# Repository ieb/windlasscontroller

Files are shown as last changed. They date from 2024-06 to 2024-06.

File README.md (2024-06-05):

# Windlass Remote Control

I have found that wire windlass switches fail at when installed at the bow due to water ingress into the switches as do sockets. So 7 years ago I used a simple 433Mhz garage door controller as a remote windlass controller. However the remote controls are not easy to use being too small, and the range is typically less than 10m which is shorter than the boat making the controller unreliable.

This project uses a JDY-40 module (typical cost < $1) which can be configured as a remote 8 channel switch. It has a claimed range of 120m, tested at 60m and uses 2.4GHz. It sleeps automatically drawing 5uA when sleeping and requires almost no external components in the controller. The base uses a second JDY-40 module with opto couplers and a G1 transistor driving a relay.  Remote is powered by a CR123A 3V lithium battery which should last several years even if left on sleeping. There is an on-off switch. No custom code, but the modules have to be programmed as transmitter and base with the same RF IDs. Code to do this is in setup. 

There are 2 schematics, one for base and one for the controller, and designs for the case and base cases. 

The PCBs are in KiCad, and were milled using pcb2gcode double sided with alignment, see createGCode.sh for the setup. Everything else is very standard.

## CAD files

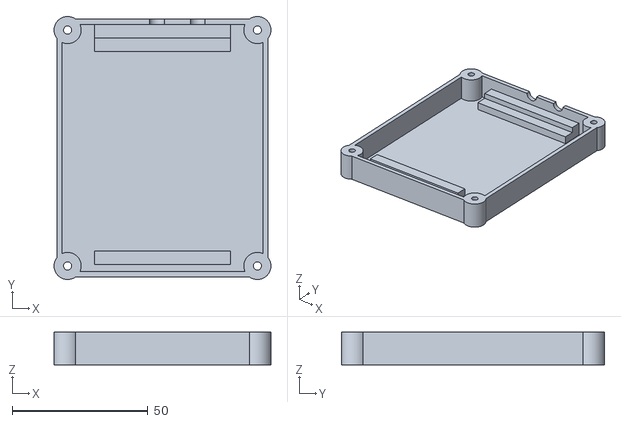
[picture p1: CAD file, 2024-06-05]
basecase/case.stl
80.0 x 97.0 x 12.0

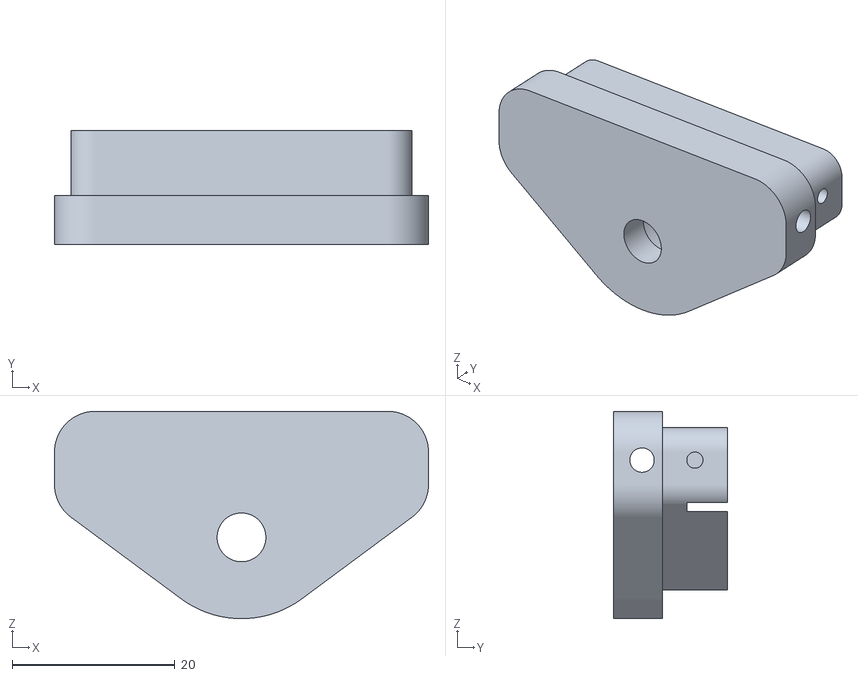
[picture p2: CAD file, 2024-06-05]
case2/cap.stl
46.0 x 14.0 x 25.5

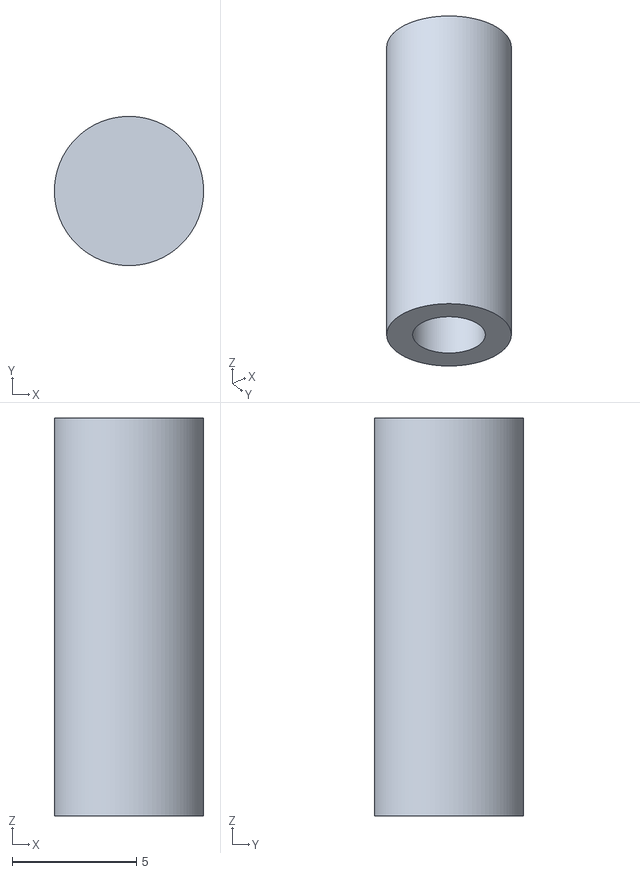
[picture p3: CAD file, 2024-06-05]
basecase/button.stl
6.00 x 6.00 x 16.0

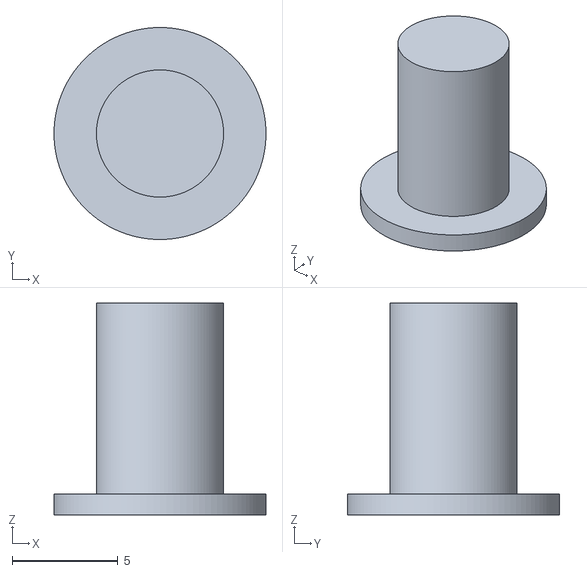
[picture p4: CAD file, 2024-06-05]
case2/onoff.stl
10.0 x 10.0 x 10.0

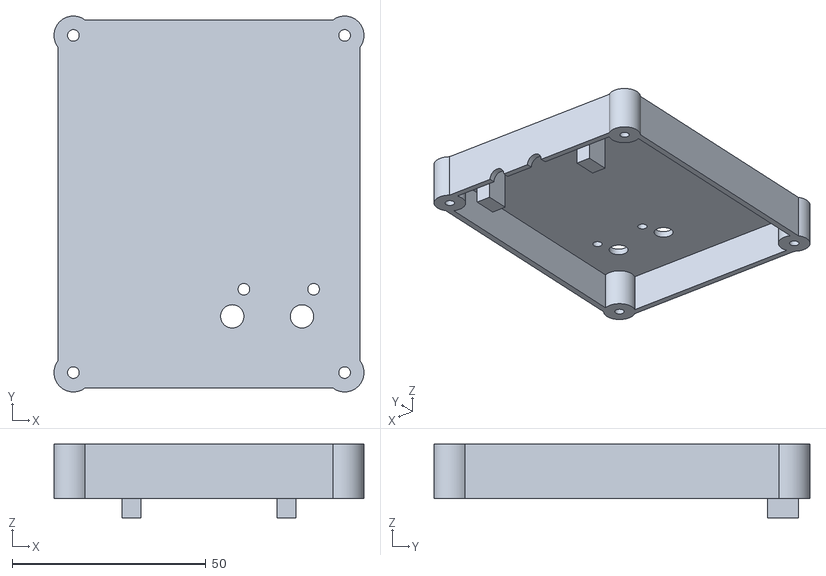
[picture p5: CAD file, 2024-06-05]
basecase/lid.stl
80.0 x 97.0 x 19.0

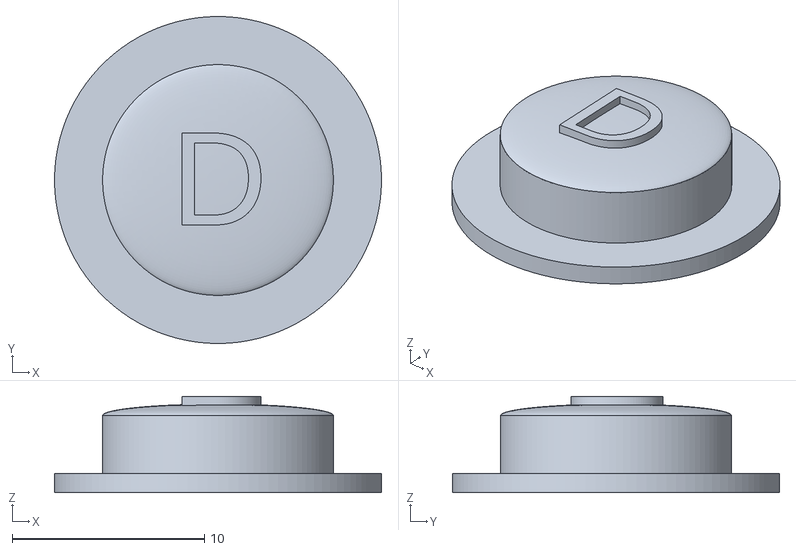
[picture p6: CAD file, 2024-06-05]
case2/down.stl
17.0 x 17.0 x 5.00

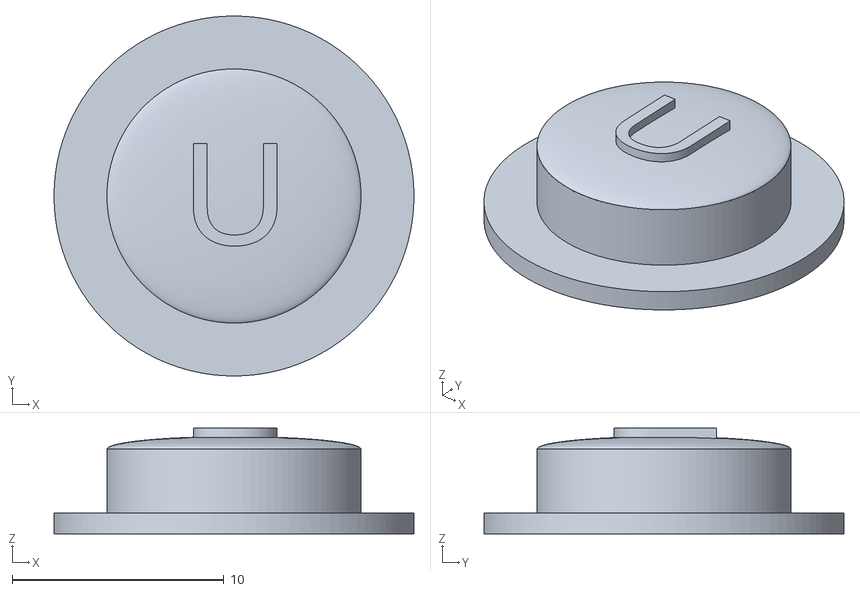
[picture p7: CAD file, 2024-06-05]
case2/up.stl
17.0 x 17.0 x 5.00

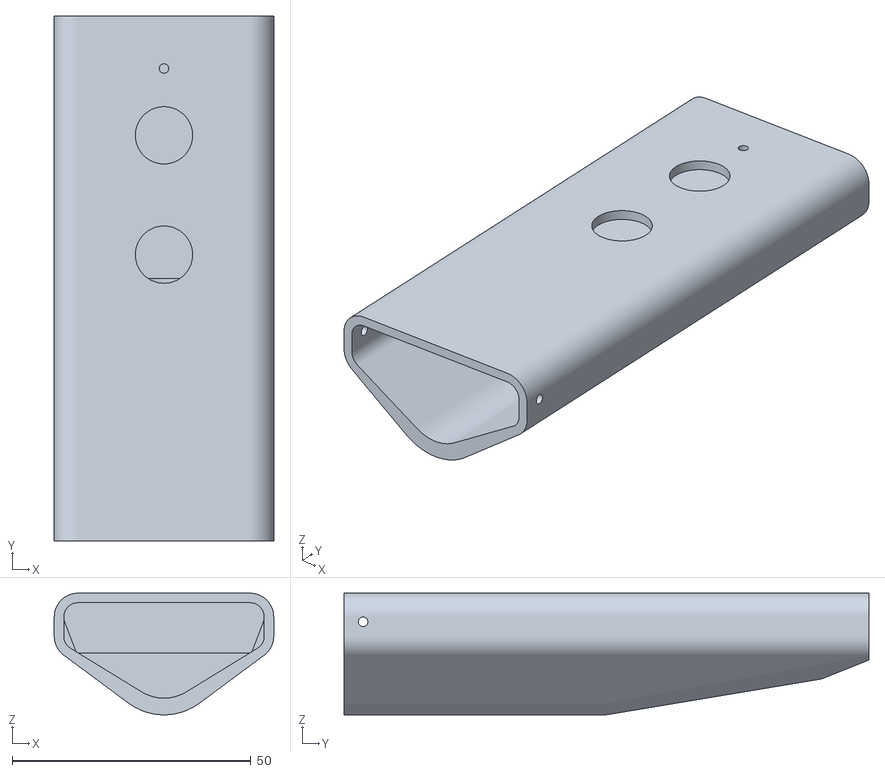
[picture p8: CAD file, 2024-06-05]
case2/case2.stl
46.0 x 110.0 x 25.5

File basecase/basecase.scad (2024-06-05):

$fn=100;




module board() {
    difference() {
    union() {
       translate([0,0,1])
        cube([60,81,2], center=true);
       // connectors
        color("blue") {
       translate([(30-17),40-9.8,15/2])
        cube([10,7.5,12], center=true);
       translate([(30-32),40-9.8,15/2])
        cube([10,7.5,12], center=true);
       // relays
       translate([(30-12),40-34,17/2])
        cube([19,19,17],center=true); 
       translate([(30-31),40-34,17/2])
        cube([19,19,17],center=true); 
        }
        
       
        // button
       translate([30-6,40-69,0])
         cylinder(d=3,h=14);
        // button
       translate([30-24,40-69,0])
         cylinder(d=3,h=14);

        // led
       translate([30-3,40-62,0])
         cylinder(d=2,h=14);
       translate([30-21,40-62,0])
         cylinder(d=2,h=14);
       
       
        
        }
    }
}
module lid(w=78,d=95,h=14,t=2) {
   difference() {
     translate([0,0,12+h/2-(t/2)]) 
      difference() {
        union() {
            difference() {
                union() {
                    cube([w-t*2,d,h], center=true);
                    cube([w,d-t*2,h], center=true);
                    translate([w/2-t,d/2-t,0])
                    cylinder(r=t,h=h, center=true);
                    translate([-(w/2-t),d/2-t,0])
                    cylinder(r=t,h=h, center=true);
                    translate([-(w/2-t),-(d/2-t),0])
                    cylinder(r=t,h=h, center=true);
                    translate([w/2-t,-(d/2-t),0])
                    cylinder(r=t,h=h, center=true);
                    

                }
                // inside
                translate([0,0,-t*2])
                    cube([w-t*2,d-t*2,h+t*2], center=true);
            }
            
            
           translate([-20,41.5,-2.5]) 
            cube([5,8,19], center=true);
           translate([20,41.5,-2.5]) 
            cube([5,8,19], center=true);

            
            // fxings
            translate([w/2-2*t,d/2-2*t,0])
                    cylinder(r=5,h=h, center=true);
            translate([-(w/2-2*t),d/2-2*t,0])
                    cylinder(r=5,h=h, center=true);
            translate([-(w/2-2*t),-(d/2-2*t),0])
                    cylinder(r=5,h=h, center=true);
                    translate([w/2-2*t,-(d/2-2*t),0])
                    cylinder(r=5,h=h, center=true);
        }
        
            translate([w/2-2*t,d/2-2*t,0])
                    cylinder(d=3,h=h+10, center=true);
            translate([-(w/2-2*t),d/2-2*t,0])
                    cylinder(d=3,h=h+10, center=true);
            translate([-(w/2-2*t),-(d/2-2*t),0])
                    cylinder(d=3,h=h+10, center=true);
                    translate([w/2-2*t,-(d/2-2*t),0])
                    cylinder(d=3,h=h+10, center=true);
    }
      cables();
    


        // button
       translate([30-6,40-69,0])
         cylinder(d=6,h=44);
        // button
       translate([30-24,40-69,0])
         cylinder(d=6,h=44);

        // led
       translate([30-3,40-62,0])
         cylinder(d=3,h=44);
       translate([30-21,40-62,0])
         cylinder(d=3,h=44);

       


    }

}

module case(w=78,d=95,h=12,t=2) {
   difference() {
   translate([0,0,(h/2)-(t/2)]) 
      difference() {
        union() {
            difference() {
                union() {
                    cube([w-t*2,d,h], center=true);
                    cube([w,d-t*2,h], center=true);
                    translate([w/2-t,d/2-t,0])
                    cylinder(r=t,h=h, center=true);
                    translate([-(w/2-t),d/2-t,0])
                    cylinder(r=t,h=h, center=true);
                    translate([-(w/2-t),-(d/2-t),0])
                    cylinder(r=t,h=h, center=true);
                    translate([w/2-t,-(d/2-t),0])
                    cylinder(r=t,h=h, center=true);
                    

                }
                // inside
                translate([0,0,t])
                    cube([w-t*2,d-t*2,h+t], center=true);
            }
            
             // pillars
            difference() {
            translate([0,-40.5,0])
            cube([50,5,10], center=true);
                translate([0,-38,0])            
                cube([55,5,3], center=true);
            }
            difference() {
                translate([0,40.5,-2])            
                cube([50,10,6], center=true);
                translate([0,38,0.5])            
                cube([55,5,4], center=true);
            }

            // fxings
            translate([w/2-2*t,d/2-2*t,0])
                    cylinder(r=5,h=h, center=true);
            translate([-(w/2-2*t),d/2-2*t,0])
                    cylinder(r=5,h=h, center=true);
            translate([-(w/2-2*t),-(d/2-2*t),0])
                    cylinder(r=5,h=h, center=true);
                    translate([w/2-2*t,-(d/2-2*t),0])
                    cylinder(r=5,h=h, center=true);
        }
        
            translate([w/2-2*t,d/2-2*t,0])
                    cylinder(d=3,h=h+10, center=true);
            translate([-(w/2-2*t),d/2-2*t,0])
                    cylinder(d=3,h=h+10, center=true);
            translate([-(w/2-2*t),-(d/2-2*t),0])
                    cylinder(d=3,h=h+10, center=true);
                    translate([w/2-2*t,-(d/2-2*t),0])
                    cylinder(d=3,h=h+10, center=true);
        }
        cables();
        
        
    }
}
module cables() {
    /*
    translate([-90,-15,10])
    rotate([0,90,0])
    cylinder(d=2,h=90);
    
    translate([-90,15,10])
    rotate([0,90,0])
    cylinder(d=4,h=90);
*/
            translate([13,0,11])
            rotate([-90,0,0])
                cylinder(d=5.5,h=55);

            translate([-2,0,11])
            rotate([-90,0,0])
                cylinder(d=5.5,h=55);


/*
    translate([-90,0,0])
    rotate([0,90,0])
    cylinder(d=4,h=90);

    color("red")
    translate([0,0,0])
    rotate([0,90,0])
    cylinder(d=7,h=90);
    */
}





difference() {
    union() {
        translate([0,0,4]) 
        board();
        color("blue") case();
        lid();
         //cables();
    }
   //translate([40,0,0])
   //cube([80,160,140], center=true);
}


//cables();
//translate([0,0,0]) 
//board();
//color("blue") case();
//lid();
//cables();

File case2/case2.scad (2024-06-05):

$fn=100;
module aaaBattery() {
    cylinder(d=10.5,h=44);
    translate([12,0,0])
    cylinder(d=10.5,h=44);
}

module aaBattery() {
    translate([8,0,0])
    cylinder(d=14.5,h=50.5);
    translate([-8,0,0])
    cylinder(d=14.5,h=50.5);
}

module cr123ABattery() {
    cylinder(d=17,h=35);
}

module cr2Battery() {
translate([0,0,0])
rotate([90,0,0])
    cylinder(d=15.6,h=27);
}
module switch(on=0,w=6,h=6) {
    cylinder(d=3.3,h=h-(on*0.8));
    translate([0,0,2]) {
        cube([w+0.3,w+0.3,4], center=true);
    }
}

module onoff(on=0) {
    cylinder(d=4,h=14-(3.5*on));
    translate([0,0,3.5]) {
        cube([7,7,7], center=true);
    }
}

module button(value) {
    difference() {
        union() {
            cylinder(d=17,h=1);
            cylinder(d=12,h=4);
            translate([0,0,4])
            scale([1,1,0.1])
               sphere(d=12);
            translate([0,0,4])
                linear_extrude(1)
                    text(value, size=5,  halign="center", valign="center");

        };
        //cylinder(d=5,h=2);
    }
}
module onoffButton() {
    difference() {
        union() {
            cylinder(d=10,h=1);
            cylinder(d=6,h=10);
            translate([0,0,9])
            scale([1,1,0.1])
               sphere(d=6);
        };
        cylinder(d=3,h=3);
        //cube([100,100,100]);
    }
}

module jdy40() {
    translate([0,0,2.5]) 
    cube([14,22,1],center=true);
}

module led() {
   translate([0,0,0])
   cylinder(d=2,h=12);
}
    


module board2() {
   translate([0,0,-2]) {
           
        translate([0,0,-1])
           cube([36,102,2],center = true);
       
   // top surface of the board is datum
         on = 0;
        translate([0,5,0]) {
           switch(on);
           translate([0,0,6.1-(on*0.8)])
               button("D");
         }
         translate([0,30,0]) {
           switch(on);  
           translate([0,0,6.1-(on*0.8)])
               button("U");
         }

         
         translate([0,17,-1.5])
           rotate([0,0,90])
               jdy40();
         
         translate([0,-44,-5.5]) {
             rotate([90,0,0]) {
                onoff(on);
                translate([0,0,11.5-(on*3.5)])
                    onoffButton();
             }
         }
         
         translate([0,44,0])
            led();
         
         translate([0,-4,-2])
          rotate([90,0,0])
            cr123ABattery();

       }
   
}


module case2() {
   difference() {
translate([0,55,-5])
  rotate([90,0,0])  {
 difference() {
     
      hull() {
          
       union() {   
        translate([0,0,55]) {
        cylinder(d=25,h=55);
        translate([18,8,0])
            cylinder(d=10,h=55);    
        translate([-18,8,0])
            cylinder(d=10,h=55);
        translate([18,4,0])
            cylinder(d=10,h=55);    
        translate([-18,4,0])
            cylinder(d=10,h=55);
        }
        
        translate([0,0,10]) {
              cylinder(d=10,h=55);
        }
        translate([18,8,0])
            cylinder(d=10,h=110);    
        translate([-18,8,0])
            cylinder(d=10,h=110);
        translate([18,4,0])
            cylinder(d=10,h=110);    
        translate([-18,4,0])
            cylinder(d=10,h=110);
        
           
       }
   
      }
      translate([0,0,55])    
      hull() {
        cylinder(d=18,h=56);
        translate([18,8,0])
            cylinder(d=6,h=56);    
        translate([-18,8,0])
            cylinder(d=6,h=56);
        translate([18,4,0])
            cylinder(d=6,h=56);    
        translate([-18,4,0])
            cylinder(d=6,h=56);
      }    
      translate([0,0,3])    
      hull() {
        translate([18,8,0])
            cylinder(d=6,h=55);    
        translate([-18,8,0])
            cylinder(d=6,h=55);
        translate([18,1,0])
            cylinder(d=1,h=55);    
        translate([-18,1,0])
            cylinder(d=1,h=55);
      }
      
      // screw holes
          translate([20,7,106])
          rotate([0,90,0])
              cylinder(d=2,h=10, center=true);
          translate([-20,7,106])
          rotate([0,90,0])
              cylinder(d=2,h=10, center=true);
    }


  }
  board2();
  }
}

module cap() {
translate([0,-55,-5])
  rotate([90,0,0]) {
      difference() {
      union() {

          hull() {
            cylinder(d=25,h=6);
            translate([18,8,0])
                cylinder(d=10,h=6);    
            translate([-18,8,0])
                cylinder(d=10,h=6);
            translate([18,4,0])
                cylinder(d=10,h=6);    
            translate([-18,4,0])
                cylinder(d=10,h=6);
       
          }
          translate([0,0,-8])    
          hull() {
            cylinder(d=18,h=13);
            translate([18,8,0])
                cylinder(d=6,h=13);    
            translate([-18,8,0])
                cylinder(d=6,h=13);
            translate([18,4,0])
                cylinder(d=6,h=13);    
            translate([-18,4,0])
                cylinder(d=6,h=13);
          } 
        }
        // button hole
        translate([0,-2.5,-9])
        cylinder(h=11,d=11);
        translate([0,-2.5,-8])
        cylinder(h=20,d=6);

        // board cutout
        translate([0,2.2,-8])
        cube([40,3,10], center=true);
        
        // scrw holes
        translate([20,7,-4])
          rotate([0,90,0])
              cylinder(d=2,h=10, center=true);
          translate([-20,7,-4])
          rotate([0,90,0])
              cylinder(d=2,h=10, center=true);

        // lanyard
        translate([00,7,2.5])
          rotate([0,90,0])
              cylinder(d=3,h=60, center=true);

        
    }
        
  }   
}

/*
board2();


difference()  {
    union() {
   cap();
   case2();
    }
  translate([0,-75,-75])
     cube([150,150,150]);
}
*/

//cap();
case2();
//button("D");
//button("U");
//onoffButton();

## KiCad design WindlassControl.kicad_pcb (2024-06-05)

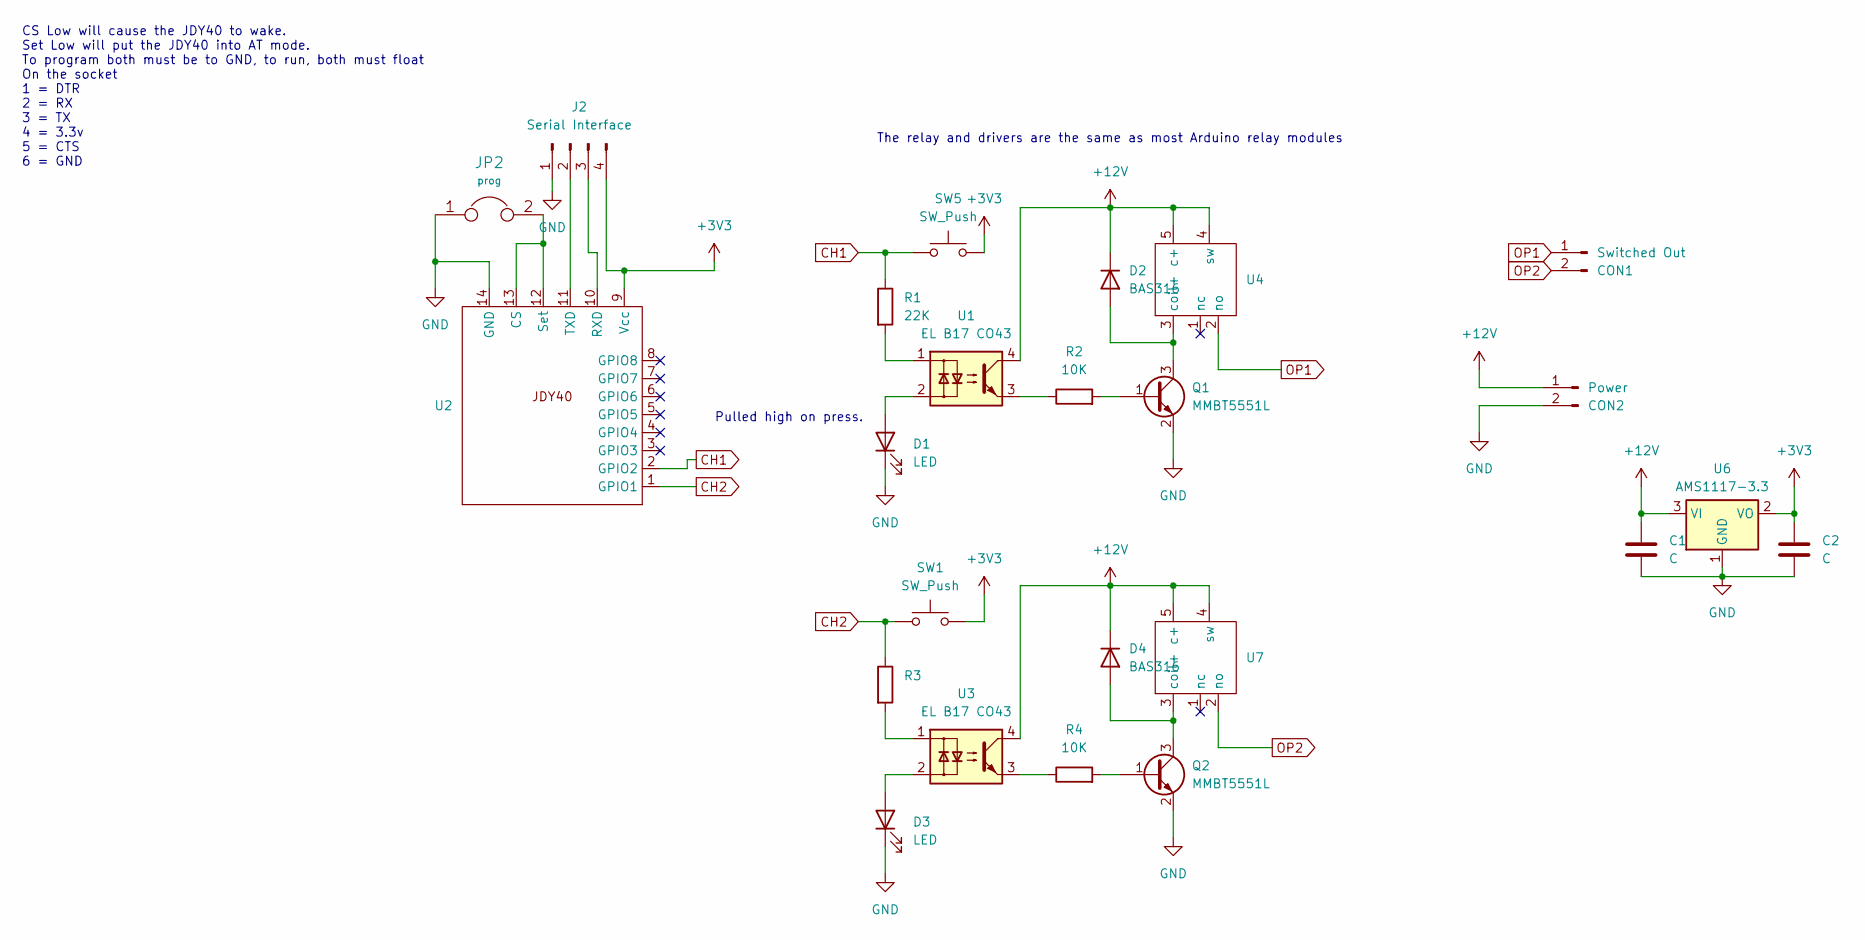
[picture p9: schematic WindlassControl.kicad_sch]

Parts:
C1, C2: C; C_1210_3225Metric
CON1: Switched Out; Molex_KK-396_5273-02A_1x02_P3.96mm_Vertical
CON2: Power; Molex_KK-396_5273-02A_1x02_P3.96mm_Vertical
D1: LED; LED_0805_2012Metric_Pad1.15x1.40mm_HandSolder
D2, D4: BAS316; LED_1206_3216Metric_Pad1.42x1.75mm_HandSolder
D3: LED; LED_0805_2012Metric
J2: Serial Interface; Harwin_M20-89004xx_1x04_P2.54mm_Horizontal
JP2: prog; SolderJumper-2_P1.3mm_Open_Pad1.0x1.5mm
Q1, Q2: MMBT5551L; SOT-23
R1: 22K; R_0805_2012Metric_Pad1.20x1.40mm_HandSolder
R2, R4: 10K; R_0805_2012Metric_Pad1.20x1.40mm_HandSolder
R3: 2.2K; R_0805_2012Metric_Pad1.20x1.40mm_HandSolder
SW1, SW5: SW_Push; SW_SPST_EVPBF
U1, U3: EL B17 CO43; OptoIsoator4pin
U2: Jdy40
U4, U7: Relay Tongling
U6: AMS1117-3.3; SOT-223-3_TabPin2

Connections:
+3V3: C2.1, J2.4, SW1.2, SW5.2, U2.9 (Vcc), U6.2 (VO)
+12V: C1.1, CON2.1, D2.1 (K), D4.1 (K), U1.4, U3.4, U4.4 (sw), U4.5 (c+), U6.3 (VI), U7.4 (sw), U7.5 (c+)
CH1: R1.1, SW5.1, U2.2 (GPIO2)
CH2: R3.1, SW1.1, U2.1 (GPIO1)
GND: C1.2, C2.2, CON2.2, D1.1 (K), D3.1 (K), J2.1, JP2.1, Q1.2 (E), Q2.2 (E), U2.14 (GND), U6.1 (GND)
unnamed: D1.2 (A), U1.2
unnamed: D2.2 (A), Q1.3 (C), U4.3 (coil+)
unnamed: D3.2 (A), U3.2
unnamed: D4.2 (A), Q2.3 (C), U7.3 (coil+)
unnamed: J2.2, U2.11 (TXD)
unnamed: J2.3, U2.10 (RXD)
unnamed: Q1.1 (B), R2.2
unnamed: Q2.1 (B), R4.2
unnamed: R1.2, U1.1
unnamed: R2.1, U1.3
unnamed: R3.2, U3.1
unnamed: R4.1, U3.3
unnamed: JP2.2, U2.12 (Set), U2.13 (CS)
OP1: CON1.1, U4.2 (no)
OP2: CON1.2, U7.2 (no)

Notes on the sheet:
The relay and drivers are the same as most Arduino relay modules
CS Low will cause the JDY40 to wake. Set Low will put the JDY40 into AT mode. To program both must be to GND, to run, both must float On the socket 1 = DTR 2 = RX 3 = TX 4 = 3.3v 5 = CTS 6 = GND
Pulled high on press.

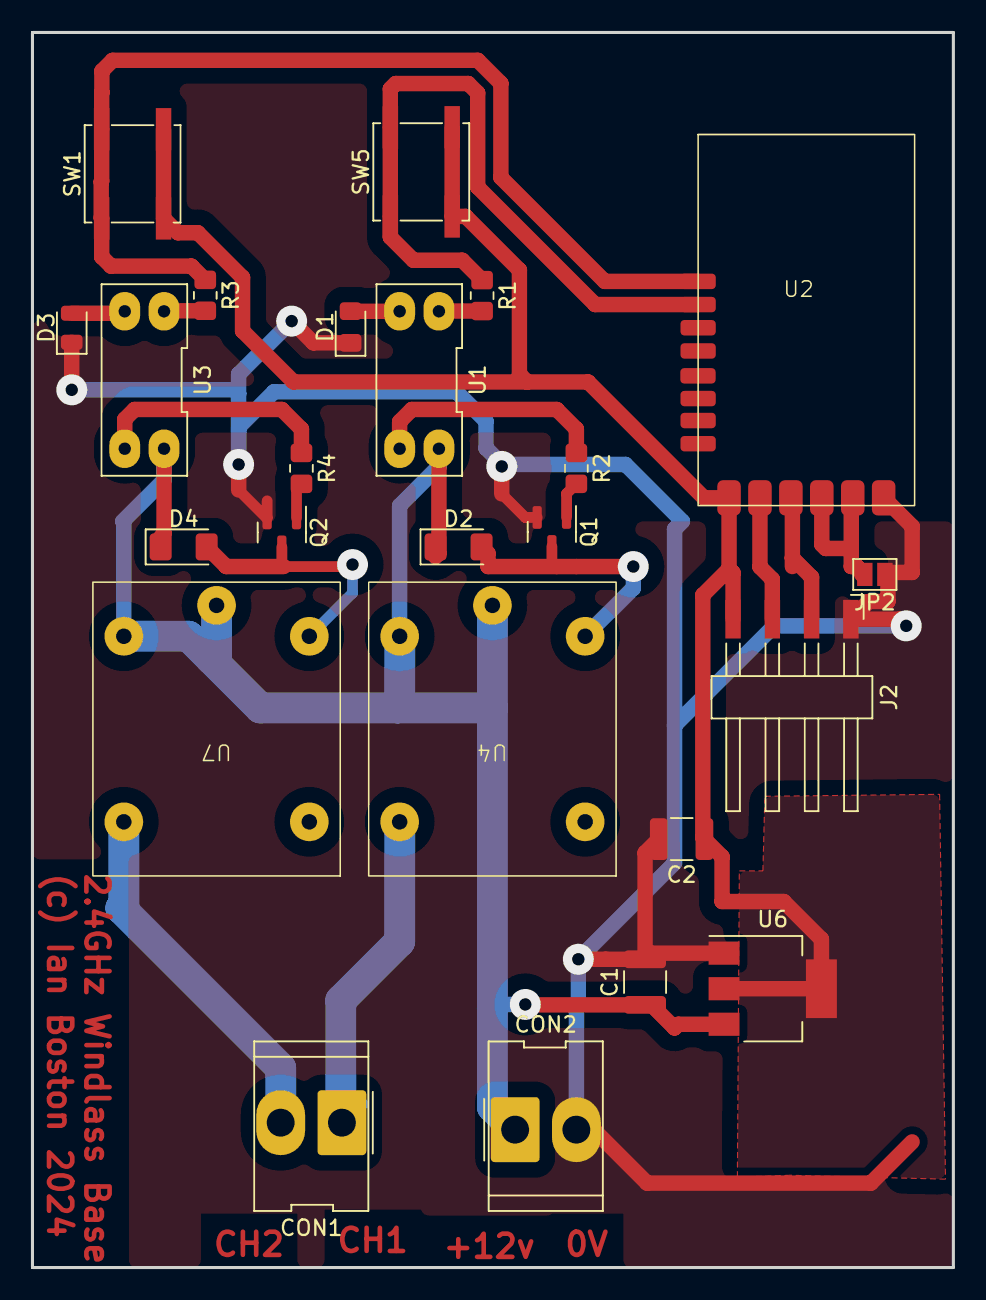
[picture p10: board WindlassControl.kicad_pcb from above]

Board: 2 copper layers, 59.6 x 79.9 mm, 24 parts (0 on the bottom side), 20 nets.

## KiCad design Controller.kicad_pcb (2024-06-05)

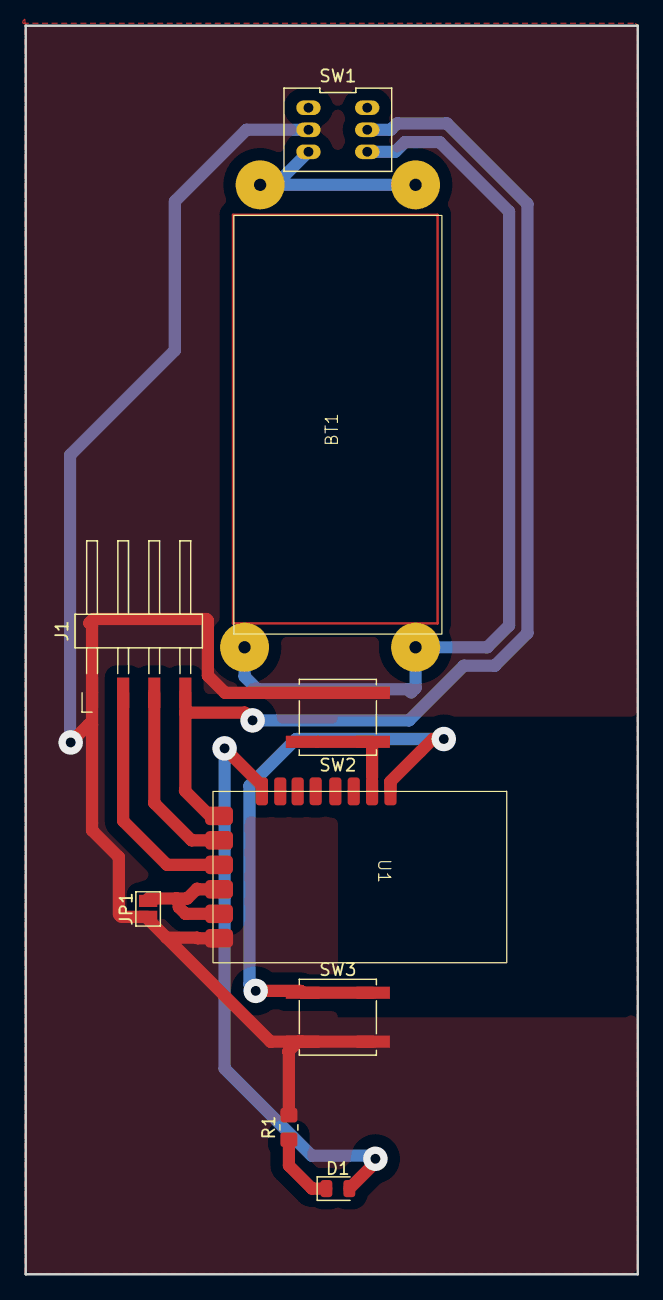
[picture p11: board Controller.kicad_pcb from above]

Board: 2 copper layers, 50.0 x 102.0 mm, 9 parts (0 on the bottom side), 11 nets.

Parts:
BT1: CR123 3V Lithium battery; CR123AHolder
D1: LED; LED_0805_2012Metric
J1: Serial Interface; Harwin_M20-89004xx_1x04_P2.54mm_Horizontal
JP1: prog; SolderJumper-2_P1.3mm_Open_Pad1.0x1.5mm
R1: 1K; R_0805_2012Metric_Pad1.20x1.40mm_HandSolder
SW1: SW_Push_DPDT; DPDT Latch Push 7x7
SW2, SW3: SW_Push; SW_SPST_EVPBF
U1: Jdy40

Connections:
Batt+: J1.4, SW1.5 (B), U1.9 (Vcc)
Batt-: J1.1, JP1.1, R1.2, SW1.2 (B), SW2.2, SW3.2, U1.14 (GND)
unnamed: BT1.1 (+), SW1.6 (C)
unnamed: BT1.2 (-), SW1.3 (C)
unnamed: D1.2 (A), U1.8 (GPIO8)
unnamed: D1.1 (K), R1.1
unnamed: J1.2, U1.11 (TXD)
unnamed: J1.3, U1.10 (RXD)
unnamed: JP1.2, U1.12 (Set), U1.13 (CS)
unnamed: SW3.1, U1.1 (GPIO1)
unnamed: SW2.1, U1.2 (GPIO2)
